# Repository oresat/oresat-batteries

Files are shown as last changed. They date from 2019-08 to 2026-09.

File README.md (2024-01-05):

# OreSat Battery Card

This is the battery card for the OreSat system. You can have up to four of these cards in any OreSat system, ID is set by resistors.

## Version History

- v1.0: We don't talk about v1 (EAGLE).
- v2.0: First true pack with 3D printed cell storage. Many small issues (EAGLE).
- v3.0: Flight ready pack, flown 2021-03-15 on OreSat0. Worked! (EAGLE).
- v3.1: Imported into KiCAD, small tweaks in process (KiCAD).

## Bill of Materials

- [PCBA](https://docs.google.com/spreadsheets/d/11vG1kWyrAjmbF5QJM-EhXmvQoF6O47japwYlHF802do/edit#gid=576852939)
- [Assembly](https://docs.google.com/spreadsheets/d/1GmZE2MR5q2XFSR2Y-65dwwPd7tem3i0CEjZBlCLeJBU/edit?usp=sharing)

## Mechanical CAD

- In [OnShape](https://cad.onshape.com/documents/5eda02ab87dc9021603c3619/w/adac4deb8bbe537007a3b153/e/e3b4fa777f54f6382aedf8d8).

## Technical Information

- 2 independent 2S1P 18650 battery packs (4 batteries total, in 2 packs). Each pack has:
   - Battery protection circuitry for charge and discharge control for each 2S1P pack
   - MAX17500 fuel gauge with cell balancing and cell temperature monitoring
- 3D printed battery holder, designed for CRP Windform SLS Nylon material (OK with Form3 Flame Retardant Resin).
- Positive battery lead disconnection switches (with room for plunger assemblies that go through OreSat +/-X rails).
- Satellite shutdown switches (!SHUTDOWN) (with room for plunger assemblies that go through OreSat +/-X rails).
- Flexible polyimide heater tapes to keep batteries above 0 C
- STM32F091 microcontroller (controlled by the OreSat Power Domain) to interface everything to the CAN bus

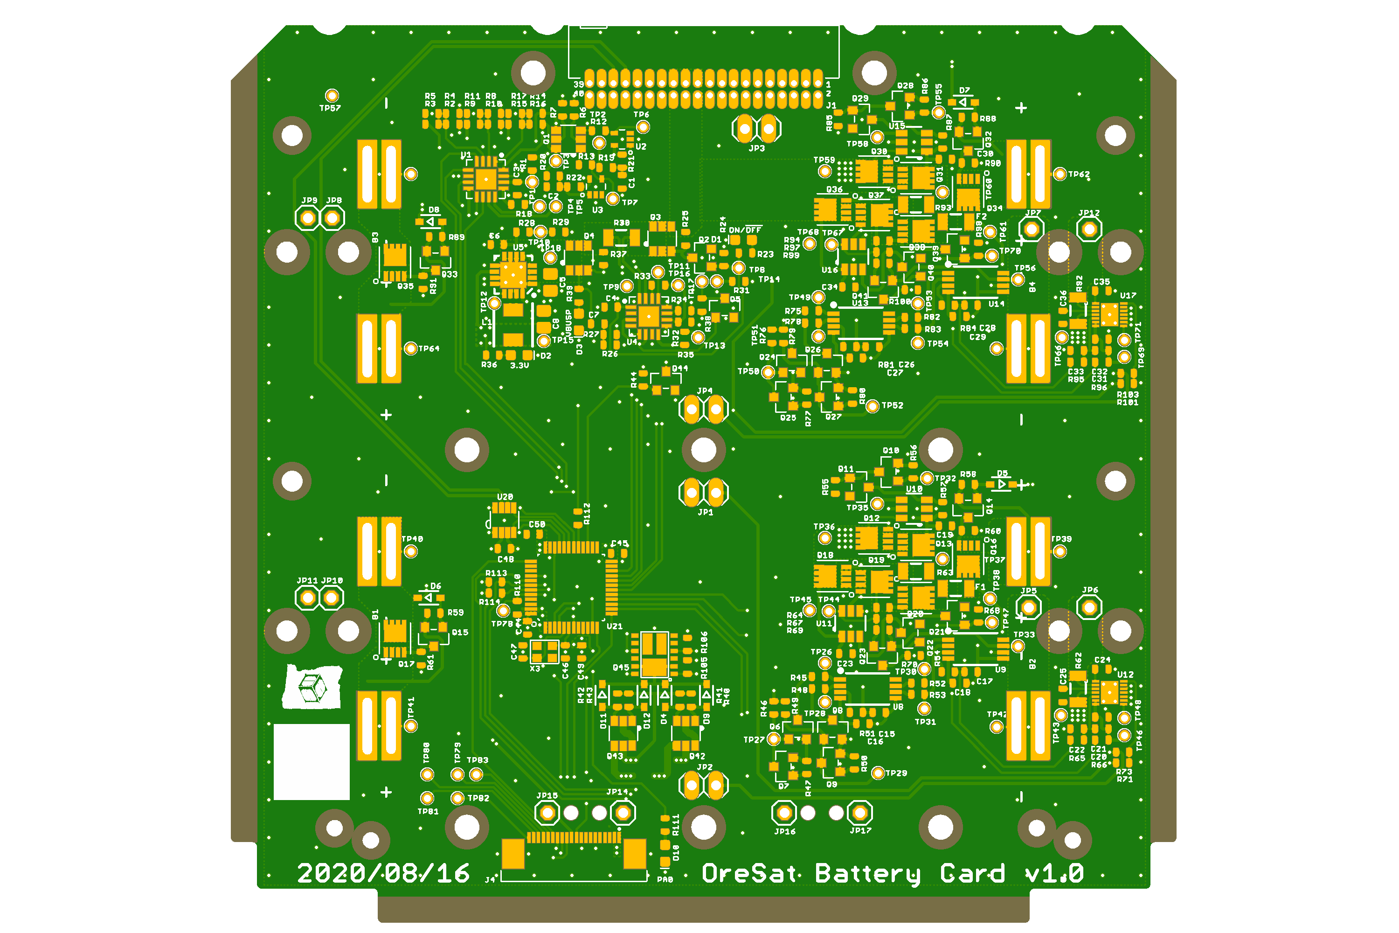
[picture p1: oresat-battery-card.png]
OreSat Battery Card v3.0 Picture


## TRANSITION DOCUMENT
Documentation is moving to [Google Docs](https://docs.google.com/document/d/1yaPGtJSM5RQG5k7sVpsDxBkVu4CHtm4LMNnisgOaNRg/edit#heading=h.gjdgxs). The rest of this readme will be integrated later.

## OreSat Vbus
OreSat main power bus is just our 2S Li Ion battery pack, which we've defined as 6.0 V minimum, 7.2 V typical, and 8.4 V maximum. Everything is directly connected to that bus, including:

- Other Oreat battery cards. For >= 2U CubeSats, you'll probably have at least two battery cards.
- All solar panels. Thus the solar panels see the direct battery voltage and can dump directly into the battery packs, thus doing _actual_ MPPT.
- All loads.

## Battery Card Topology
Confusingly, Each OreSat battery card has 2 independent battery packs on it. Each pack is made of a 2S1P 18650 LiPo cell pack. So it's a 2x2S1P if you will. Despite this, each card is independent and the OPD is fully capable of functioning with only one active card.

We decided to separate the packs instead of combining them into a single 2S2P pack for the sake of redundancy, we can lose one cell and the other pack can still provide power to the OPD, as opposed to losing an entire card from a single cell failure.  This design does come with the added drawbacks of extra overhead in the form of requiring more charge protection and fuel gauge circuitry.

## Charge/Discharge Protection
We are using Ablic S8209 to monitor our cell voltage levels and disable charging if the cell voltage goes above the predetermined overcharging threshold or disable discharging if the cell voltage goes below a predetermined discharging threshold.

The S8209 has two inputs that, if activated, will trigger the either the over-charge or under-charge protection to activate.  This allows us to daisy chain these chips together, so that each cell has its own charge protection IC.  It also allows us to connect them to a GPIO on an onboard microcontroller so that we can manually disable charging or discharging functionality if needed.  Below is a state diagram that depicts the desired behavior of our charging and discharging protection circuit

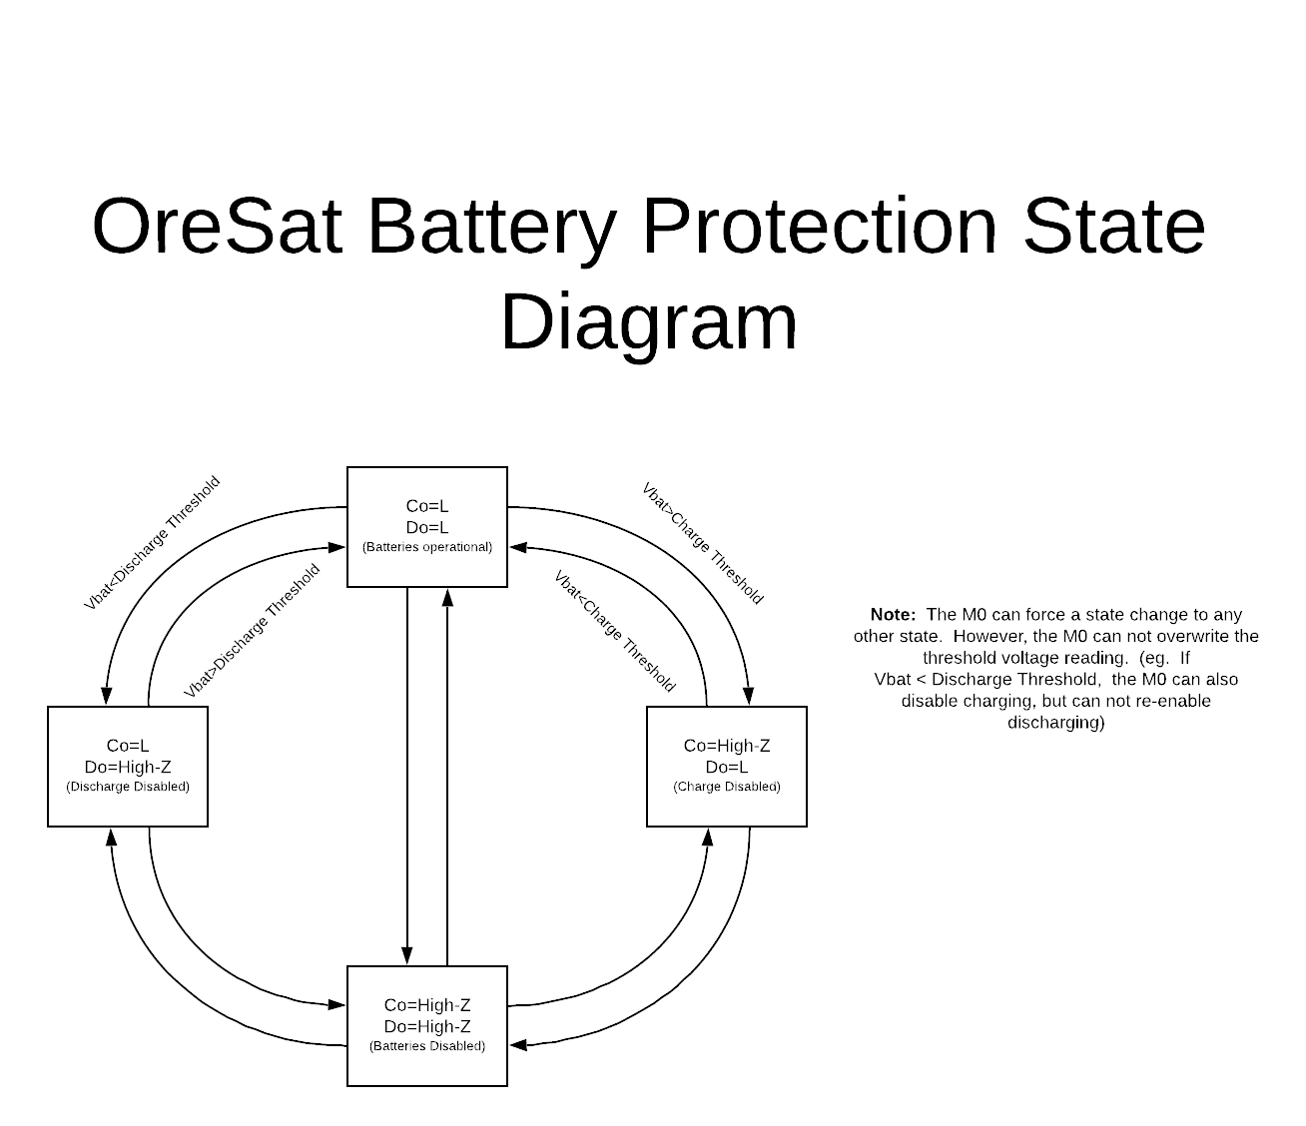
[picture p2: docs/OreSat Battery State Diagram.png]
Battery Disable State Diagram


The output of the S8209 uses an internal N-channel MOSFET, which has the potential to latch from radiation exposure.   To combat this, we have P-channel MOSFETS in series with the VDD of each S8209, the gate of the MOSFET is connected to our onboard microcontroller, so that we can periodically power cycle the S8209 and clear the N-channel latch.

The actual control of charge and discharge are done using Linear LTC4412 ideal diode controllers. Totally bizarre, but indepdenently controllable!

## Fuel Gauge and Cell Health Monitoring
Each 2S1P battery back will have two MAX17205 fuel gauges to monitor the packs current state of charge, and the long term health of the battery.  Each MAX17205 will be reporting both the direct State of charge (in mAh) and the percentage over I2C to our M0, compensating for factors such as cell degradation and temperature ranges.  We are still testing the accuracy of the MAX17205's compensation algorithm's for extreme charge levels and temperature in our lab.  At this point we don't know how much we should be relying on these compensation algorithms, they could be amazing! Or horrible! We don't know! Yay science!

Each fuel gauge is also monitoring the battery temperatures with a single internal sensor and two external thermistors (we are still determining the best position for these thermistors).  This gives us a wackton of data which is good because we are data hoarders.

Finally the MAX17205 also does cell balancing, which we'll enable while charging.

## Heaters
Thermal models of both 1U and 2U CubeSats show an average "passive" battery temperature of ~ -10 C). That's not good. We can't charge the battery below 0 C. So we've added heaters to heat up the batteries when charging if necessary.

We're using two Minco HK6903 heaters in parallel. They have "vacuum OK" (apparently?) urethane PSA that we'll use to attach them to the batteries. Note that they're 12.7 x 100 mm, and each heater goes across both batteries. At 49 ohms +/- 10% each, that's 25 ohms in parallel. Unclear on the heater's tempco. We'll ignore for now.

- At 8.4V, that's 336 mA = 2.8 W (at 100% DC)
- At 6.0V, that's 240 mA = 1.4 W (at 100% DC)
- We can of course PWM them and reduce the power as necessary

With that much current draw, we're going to need to modify the OPD circuit breaker to allow more current.

## Batteries

- Tenergy model "30005-0 (ICR 18650-2600, LR1865SK)"
- Rated at 2600 mAh
- Max voltage: 4.2 V
- Typical voltage: 3.6 V
- Minimum voltage: 2.75 V
- Maximum charge current: 1.25 A
   - 0 - 45 C only
- Maximum discharge Current:
   - -20 - 5 C = 1.25 A
   -  5 - 45 C = 5 A
   - 45 - 60 C = 3.75 A

### Temperature

Just to summarize the battery temperature operational range:

- Cell temperature < -20 C -- DEAD
- Cell temperature < 0 C -- DISCHARGE ONLY
- Cell temperature < 45 C -- NORMAL OPERATION
- Cell temperature > 45 C-- DISCHARGE ONLY
- Cell temperature > 60 C-- DEAD

### Cell failure (short)

- Short will plummet battery to < 2.5V (Vlvco) and S-8209 will disconnect the battery from discharging but not charging

## Battery pack behaviors (circuitry + firmware)

- Automatic discharge if > 6.0 V
- Automatic slow charge if < 8.4 V
- Fast charge if battery pack within ~ 0.5 V of other batteries

## Hacking the OPD Circuit Breaker

The OPD circuit breaker is supposed to trip at 300 mA without any division at the current output. Since the headers could pull up to 336, we need to probably go up to that plus 50 mA. So we put in a 10K and 20K to make a 0.66 divider and an N CH MOSFET to turn on the divider on the signal "MOARPWR". Asserting MOARPWR should give you up to 400 mA.

## LICENSE

Copyright Portland State Aerospace Society 2020.

This documentation describes Open Hardware and is licensed under the CERN OHL v. 1.2.

You may redistribute and modify this documentation under the terms of the CERN OHL v.1.2. [http://ohwr.org/cernohl](http://ohwr.org/cernohl). This documentation is distributed WITHOUT ANY EXPRESS OR IMPLIED WARRANTY, INCLUDING OF MERCHANTABILITY, SATISFACTORY QUALITY AND FITNESS FOR A PARTICULAR PURPOSE. Please see the CERN OHL v.1.2 for applicable conditions.

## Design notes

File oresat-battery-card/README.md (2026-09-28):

# "oresat-proto-card"

This is the "prototype" card for OreSat, meant to pioneer future cards and test the backplane, and be an 
easy way to hack in functionality. NOT MEANT FOR FLIGHT.

## Features

- Populates the two 1.27 mm connectors from the backplane.
- Populates all three SMPM RF connectors from the backplane.
- Standard TPS63070-bsaed buck/boost SPS (Vin = 2.5 to 7 V, Vout = 3.3V)
- Has our standard/favorite STM32F042K6 microcontroller.
   - With SWD, UART (FTDI), and CAN (to the backplane).
- Has lots of breakouts, but DO NOT POPULATE THE 0.1 IN CONNECTORS, THEY'RE TOO TALL!!!

OreSat ProtoCard Picture

## Connector information

- Main 1.27 mm connector ("Center" connector)
   - Samtec TFM-120-01-L-D-RA
   - https://www.digikey.com/products/en?lang=en&site=US&keywords=TFM-120-01-L-D-RA
   - Drawing: http://suddendocs.samtec.com/prints/tfm-1xx-xx-xxx-d-xxx-mkt.pdf
   - Brochure: http://suddendocs.samtec.com/catalog_english/tfm.pdf
   - 3D CAD: https://www.samtec.com/partnumber/tfm-120-01-l-d-ra?vendor=digikey#technical
   - Notes: the -RE1 model is better because of the solder stakes, but the female connector doesn't fit! The stakes get in the way :(

- Auxiliary 1.27 mm ("alt-left" connector)
   - Samtec TFM-110-01-L-D-RA

- RF (70 cm, L band, S band) conenctors
   - Card
      - Molex 73300-0030 (possible replacement is 73300-0020 but it has full detent that we don't want)
      - SMPM Connector Plug, Male Pin 50 Ohm Board Edge, Cutout; Surface Mount Solder, smooth bore
      - Molex w/3D: https://www.molex.com/molex/products/datasheet.jsp?part=active/0733000030_RF_COAX_CONNECTORS.xml
   - Barrell (connects card to backplane)
      - Molex 73300-0220 (alt but slightly different lengths: -0223, -0228)
      - SMPM female to female barrel adapter 
      - RF Adapters - In Series SMPM JACK/JACK BULLET .21IN
      - Molex w/3D: https://www.molex.com/molex/products/datasheet.jsp?part=active/0733000220_RF_COAX_CONNECTORS.xml

## OreSat Power Domain (OPD)

You can find more design information on the OPD [here](https://docs.google.com/document/d/1NOkO6gGEJUFRpOrkwClRlZlzWuTLteq6fP9LPf_Ez0M/edit?usp=sharing).

## LICENSE

Copyright Portland State Aerospace Society 2018.

This documentation describes Open Hardware and is licensed under the CERN OHL v. 1.2.

You may redistribute and modify this documentation under the terms of the CERN OHL v.1.2. [http://ohwr.org/cernohl](http://ohwr.org/cernohl). This documentation is distributed WITHOUT ANY EXPRESS OR IMPLIED WARRANTY, INCLUDING OF MERCHANTABILITY, SATISFACTORY QUALITY AND FITNESS FOR A PARTICULAR PURPOSE. Please see the CERN OHL v.1.2 for applicable conditions.

## Version Information

Version | Date       | Notes
--------|------------|-------------------------
3.0     | 2018/11/22 | Big changes in structure, mostly springs. Changed RF connectors to SMPM. Optimized layout for more proto area. 
2.0     | 2018/03/?? | New 1.27 mm connectors, again.
1.0     | ??         | New connectors.

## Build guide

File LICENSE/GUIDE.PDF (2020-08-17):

# Guide to the CERN OHL v.1.2

This document contains guidelines on how to apply the CERN OHL v.1.2 to a given hardware design, and on the use of hardware designs licensed under the CERN OHL v.1.2.

How to apply the CERN OHL v.1.2 to a hardware design Pre-requisite:

Authorship/ownership of the design must be clear and undisputed. Only the legal owner of the rights in the hardware design may decide under what conditions to make it available. If ownership is vested in more than one person/entity, there must be an agreement among the owners to release the hardware design as open hardware, and under the CERN OHL in particular.

The hardware design documentation and files package

Pack all your hardware design documentation files (schematics, layout...) as well as the documents listed below in an archive file. This will ensure the licensee downloads everything in one go. It is best to archive the files using a format everybody can open. Schematics and layouts should be included in both source form and a format readable by everybody, such as pdf.

The following documents must be distributed together with the hardware design documentation:

- Document containing the CERN OHL v.1.2 (e.g. LICENSE.PDF)
- This Guide
- Text files (plain ASCII file), where information can be added to but not removed from, listing:
- Contact point wishing to receive information about manufactured Products (see section 4.2) (e.g. PRODUCT.TXT);
- Modifications made by Licensee (see section 3.4.b) (e.g. CHANGES.TXT)

What to do with the hardware design documentation

Include in the hardware design documentation, for instance as a header, the following elements (see section 3.1 CERN OHL v.1.2):
- a copyright notice reflecting actual ownership;
- a notice that the hardware design documentation is licensed under the CERN OHL v.1.2, possibly with a link to http://ohwr.org/cernohl where the licence texts are hosted:
- “Licensed under CERN OHL v.1.2 or later”
- “Licensed under CERN OHL v.1.2”;
- a disclaimer of warranties;
- a Documentation Location if you wish to specify one;

The following is an example of header if CERN is the Licensor:

Copyright CERN 2013.

This documentation describes Open Hardware and is licensed under the CERN OHL v. 1.2.

You may redistribute and modify this documentation under the terms of the CERN OHL v.1.2. (http://ohwr.org/cernohl). This documentation is distributed WITHOUT ANY EXPRESS OR IMPLIED WARRANTY, INCLUDING OF MERCHANTABILITY, SATISFACTORY QUALITY AND FITNESS FOR A PARTICULAR PURPOSE. Please see the CERN OHL v.1.2 for applicable conditions

Include in a part of the Documentation corresponding to a visible part of the Product (e.g. silkscreen or top copper for a Printed Circuit Board):

- the licence notice: “Licensed under CERN OHL v.1.2”
- Do not include the CERN logo or the copyright notice
- the Documentation Location if you wish it to appear on the Product, thus enabling all subsequent recipients of the Products to find the Documentation.

How to deal with hardware designs licensed under the CERN OHL v.1.2
Generally speaking, you must always comply with any obligations applying to a particular design (detailed in a contract or accompanying licence). If you receive hardware designs licensed under the CERN OHL v.1.2, the obligations are to:
- Keep intact all the copyright and trademark notices and Documentation Location notices that are on the hardware design documentation;
- Keep intact the references to the CERN OHL v.1.2;
- Keep intact the disclaimer of warranties.

If you modify hardware design that you received from someone else that is licensed under the CERN OHL v.1.2, you must

- Keep intact all the notices referred to above;
- Include notices that you have modified the hardware designs, detailing what modifications where made (e.g. in a CHANGES.TXT file);
- Add the appropriate copyright notice and Documentation Location to the modifications that were made;
- license the modifications under the CERN OHL v.1.2 if you distribute them.

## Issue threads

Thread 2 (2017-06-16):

Surface mount 2.54 debug header pins

kwilsonpdx, 2017-06-16:
Please add surface mount header pins for VBATT/Solar Vin/Grounds/CANH/CANL/UARTRX/UARTTX. You could route these to one 2x8 or separate around board as layout permits. These can be DNP for flight.

austinjoseph, 2017-06-21:
Added to a single debug 2x8 2.54mm pinheader.  Will go out in next commit.

Closed 2017-06-21.

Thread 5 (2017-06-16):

Test issue: Suggest adding Thermocouple attach point for analysis

kwilsonpdx, 2017-06-16:
To test heater performance suggest adding at least one thermocouple attach point. I'm thinking a #2 through hole. Open to suggestions on implementation.

(I'm not sure the internal battery thermistor is going to give us what we need to test the resistive heater).

Closed 2020-08-17.

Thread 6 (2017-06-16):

Review source for SCL/SDA pullup resistors

kwilsonpdx, 2017-06-16:
Should the source be VBATT+ not VSOLAR?

austinjoseph, 2017-06-21:
Ha!  You're right.  If we run it from the solar panels we lose telemetry when that panel is on the dark side.  I've fixed this issue and will push it soon.

Closed 2017-06-21.

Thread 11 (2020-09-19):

Add 100k Pullups to the LT4412 STAT pin

davidalay, 2020-09-19:
the pin is an open collector, when active it can sink max of 10uA of current so pullup must be >10k

andrewgreenberg, 2021-04-08:
Nope! The uC will use weak pullups to 3.3V for these puppies. I'll tell Dave.

Closed 2021-04-08.

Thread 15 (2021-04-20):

Fixes to the battery board based on v2.1 assembly

andrewgreenberg, 2021-04-20:
Ref designators : C29, C28, R27, R17, R14
TP12 shorts to the inductor - move it!

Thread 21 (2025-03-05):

MAX17205 isn't calculating the correct capacity

andrewgreenberg, 2025-03-05:
This is probably a firmware issue, but the MAX17205 is not calculating the correct capacity of the battery pack. Voltage and current seem to be working, and the pack "factory" capacity is correct, but it's not updating the capacity in any meaningful way. Is the MAX losing it's mind every time we hit the !SHUTDOWN circuit because it's disconnected from the battery? And it wasn't designed for that? Have we misconfigured it some way? Is it that the battery is never turned off long enough for the MAX to get a Voc reading?

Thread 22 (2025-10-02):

POUT signal not routed to an analog input

plskeggs, 2025-10-02:
The following is about the STM32F091 version of the battery card.

The POUT signal that can measure power/current draw from OPD goes to PA8, and is an analog signal 0-1.2v according to the schematic. However, PA8 does not connect to any ADC channel in the F091. The only unused ADC-capable pin is PA6, pin 16. As a result, the Oresat 0 and 0.5 firmware does not monitor this signal.

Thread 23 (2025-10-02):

F091 not labelled on schematic

plskeggs, 2025-10-02:
It is missing "U21 ST32F091CCT7."

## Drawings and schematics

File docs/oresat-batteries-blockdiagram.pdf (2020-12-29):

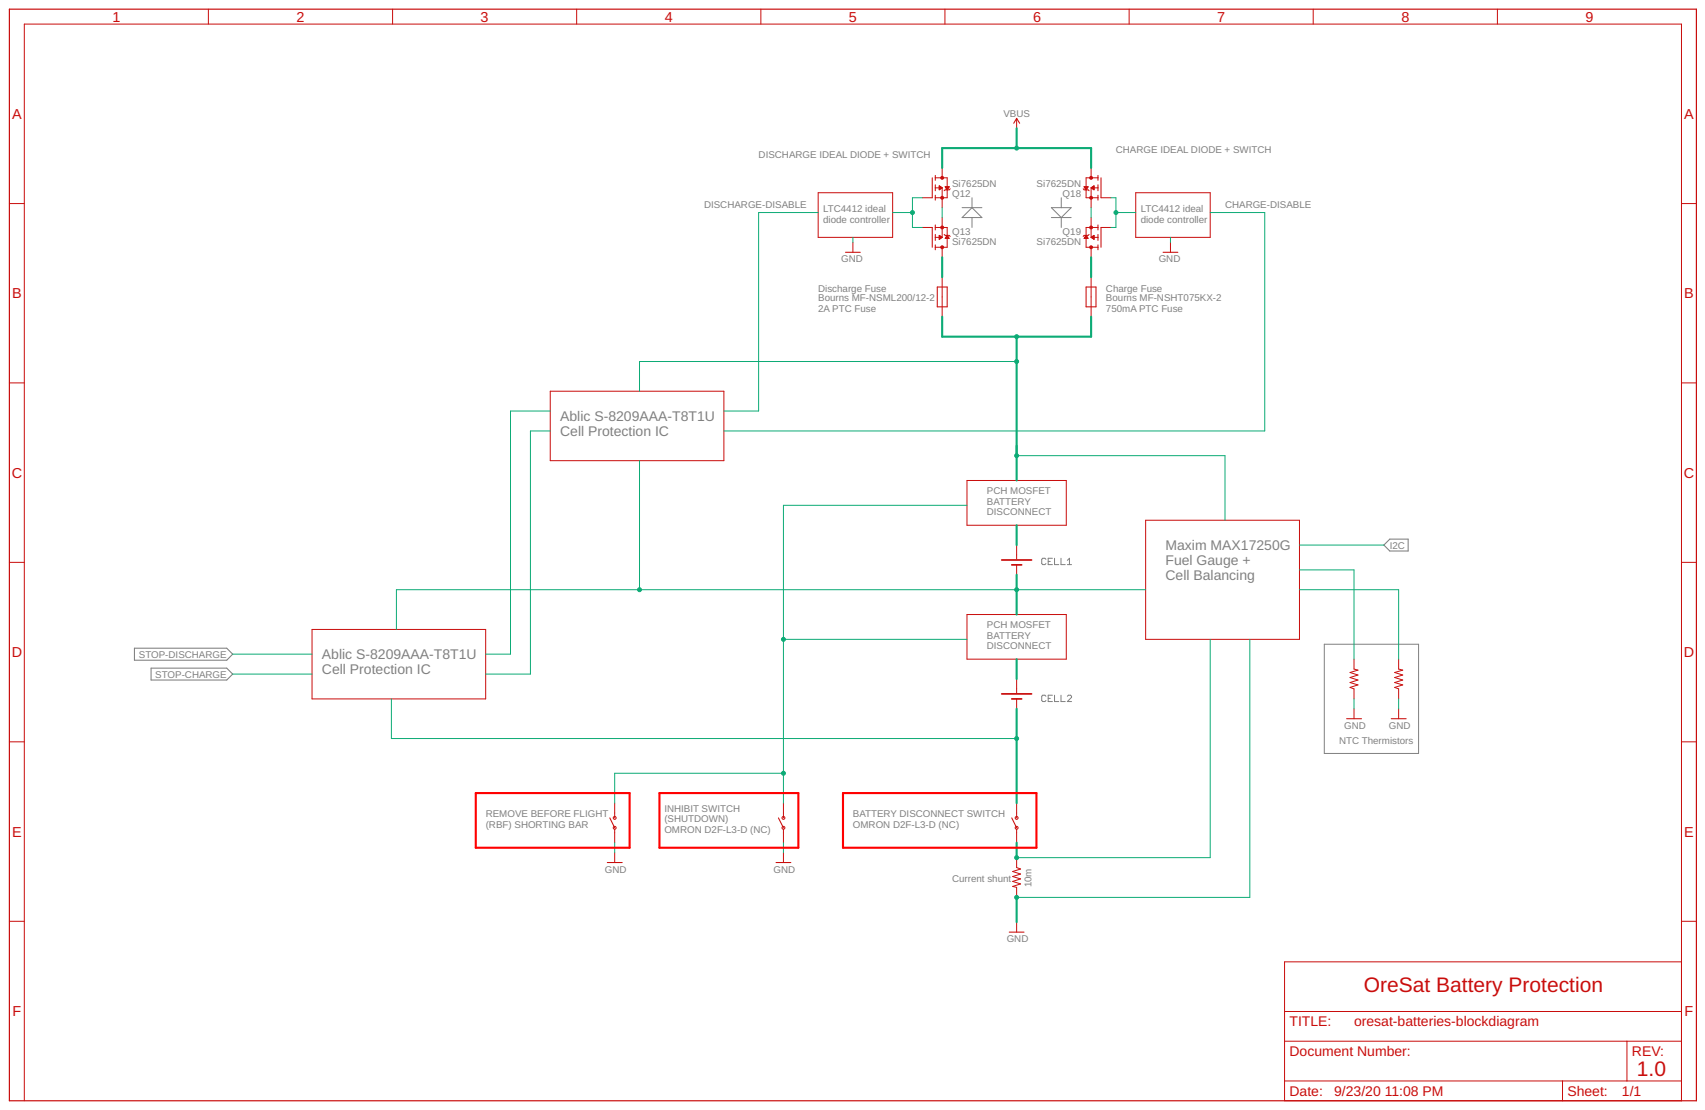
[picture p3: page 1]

CHARGE IDEAL DIODE + SWITCH DISCHARGE IDEAL DIODE + SWITCH

LTC4412 ideal diode controller Bourns MF-NSML200/12-2

PCH MOSFET BATTERY DISCONNECT

Maxim MAX17250G
Fuel Gauge + Cell Balancing

NTC Thermistors BATTERY DISCONNECT SWITCH OMRON D2F-L3-D (NC)

(SHUTDOWN) OMRON D2F-L3-D (NC) REMOVE BEFORE FLIGHT
(RBF) SHORTING BAR

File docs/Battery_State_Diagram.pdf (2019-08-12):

# OreSat Battery Protection State Diagram

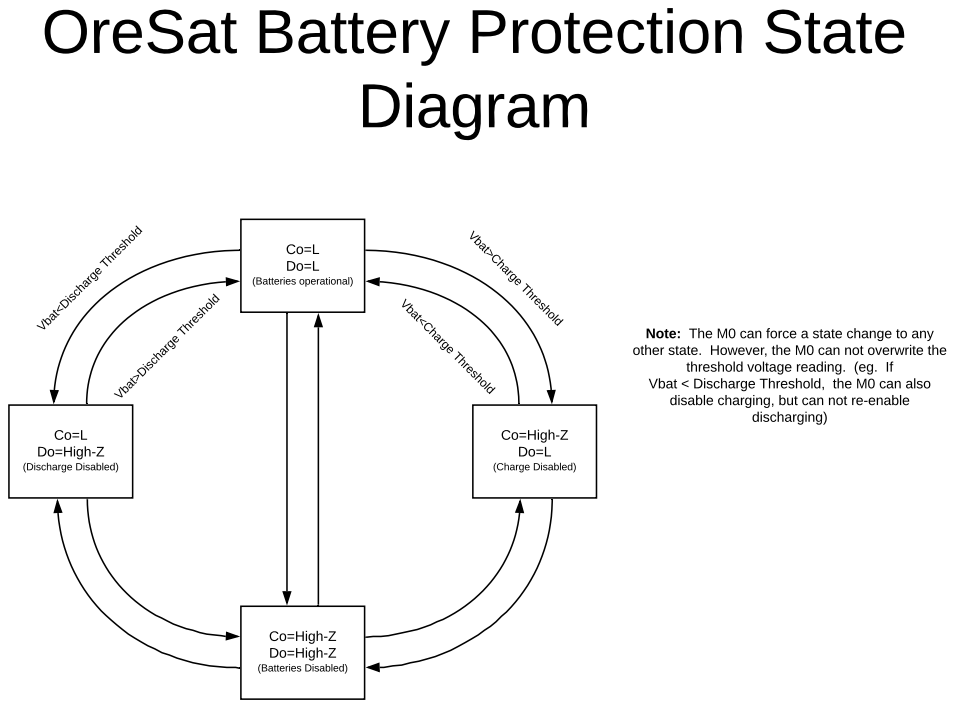
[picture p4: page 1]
Co=L Do=L (Batteries operational); Co=L Do=High-Z (Discharge Disabled); Co=High-Z Do=L (Charge Disabled); Co=High-Z Do=High-Z (Batteries Disabled); discharging)

Vbat>Charge Threshold

Vbat<Charge Threshold

Vbat<Discharge Threshold

Note: The M0 can force a state change to any
other state. However, the M0 can not overwrite the

threshold voltage reading. (eg. If
Vbat < Discharge Threshold, the M0 can also
disable charging, but can not re-enable

Vbat>Discharge Threshold

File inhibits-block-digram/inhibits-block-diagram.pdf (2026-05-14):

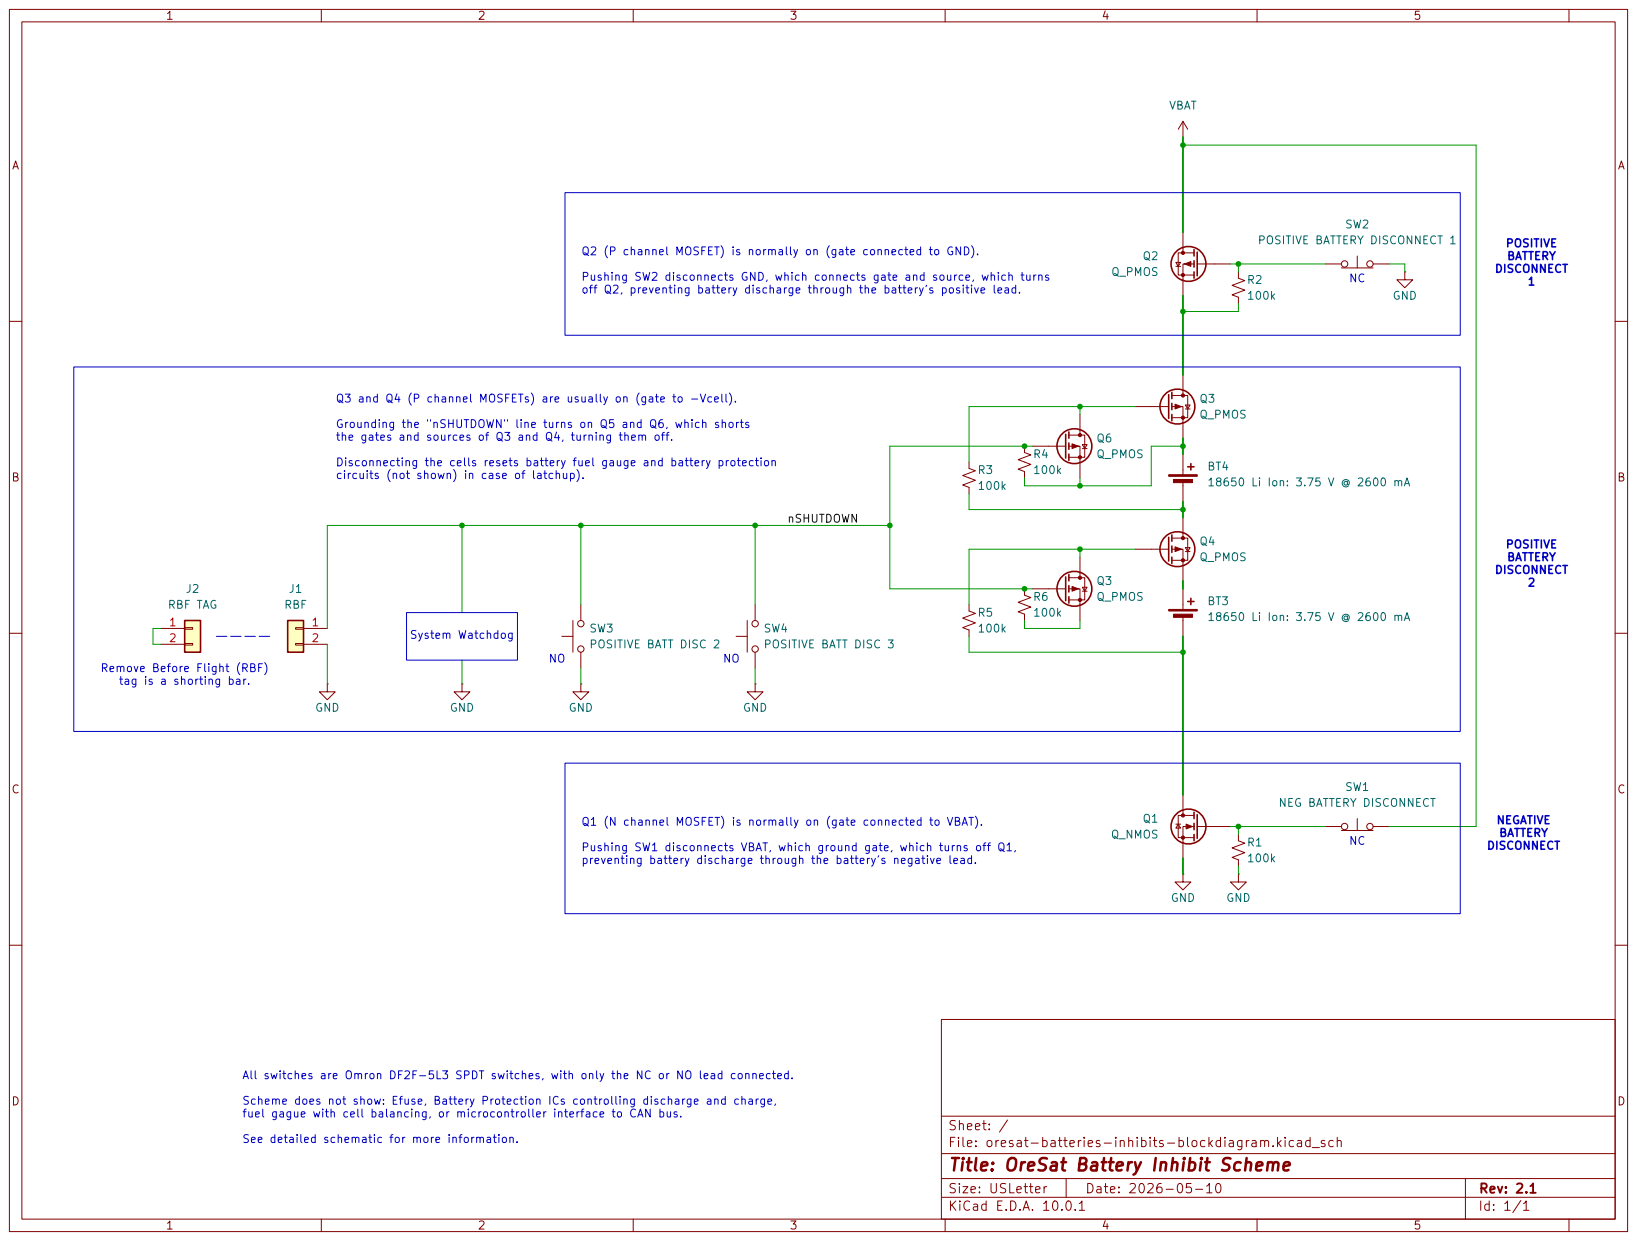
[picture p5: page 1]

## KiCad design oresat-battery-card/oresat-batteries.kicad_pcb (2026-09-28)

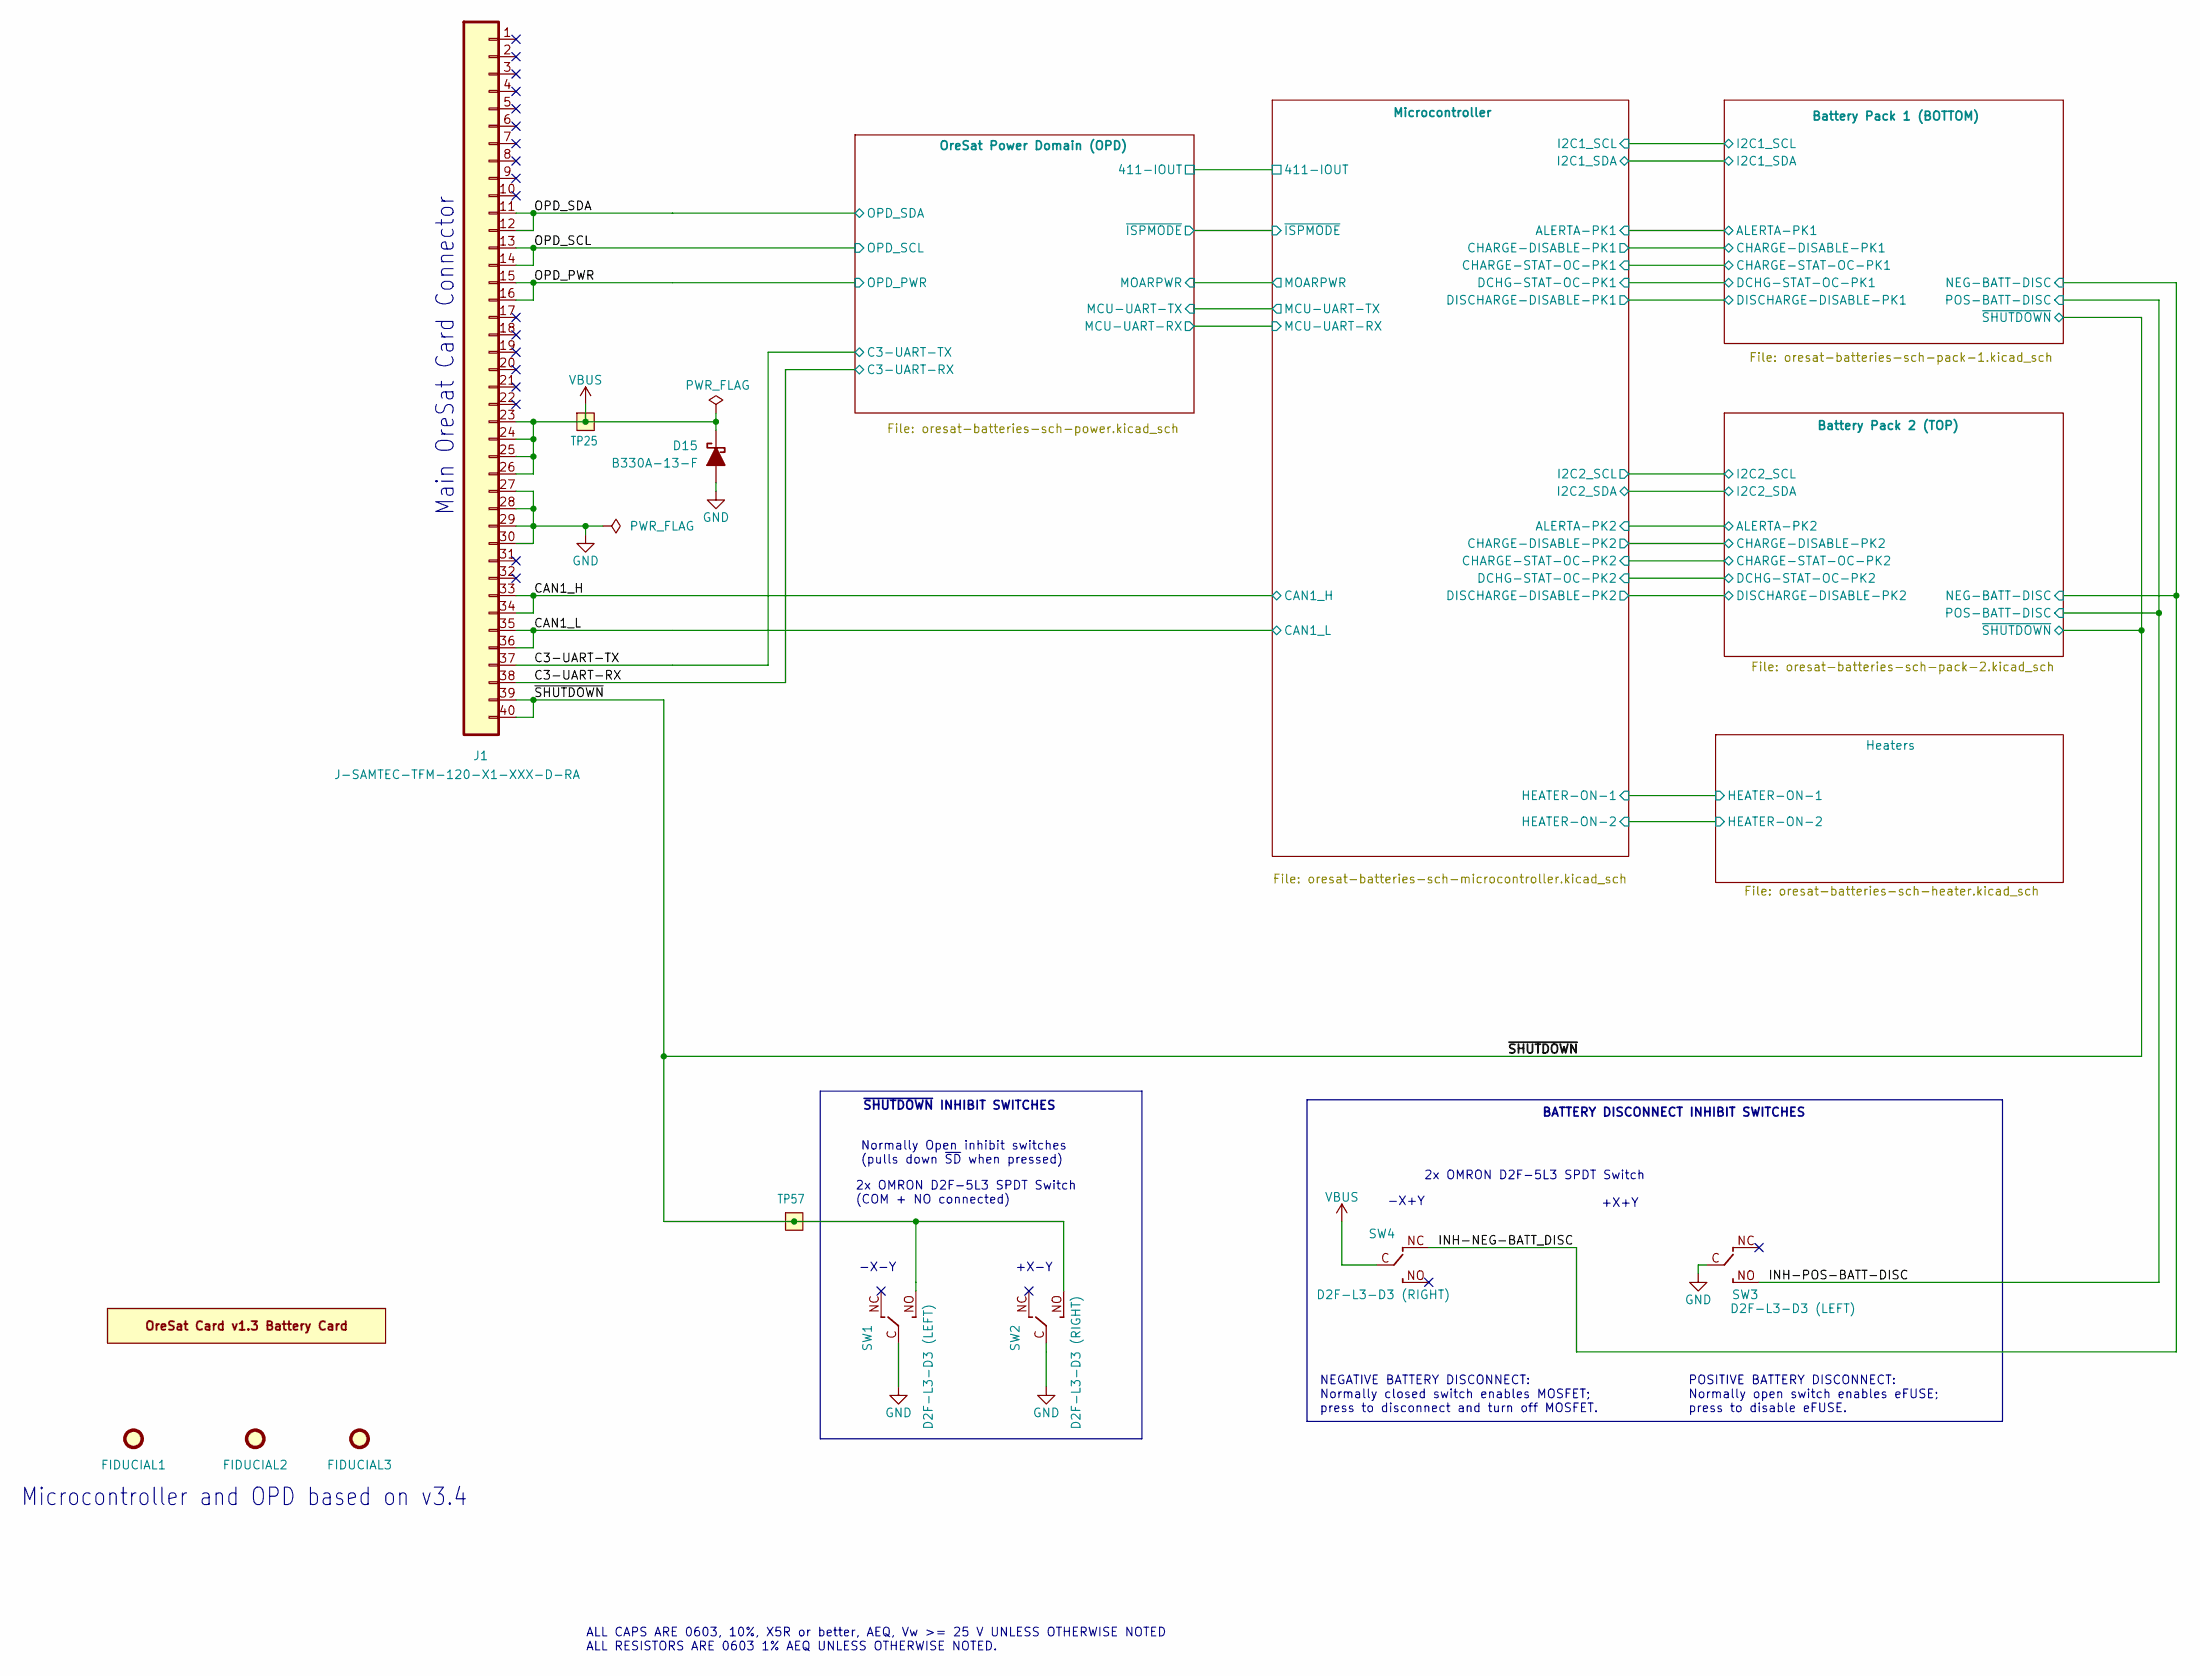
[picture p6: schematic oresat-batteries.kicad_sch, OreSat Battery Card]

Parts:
D15: B330A-13-F; D_SMA; MPN B330A-13-F
FIDUCIAL1, FIDUCIAL2, FIDUCIAL3: FIDUCIAL-1.0X2.0; Fiducial_1mm_Mask2mm
J1: J-SAMTEC-TFM-120-X1-XXX-D-RA; MPN TFM-120-01-L-D-RA
PCB1: ORESAT-CARD-V1.3-BATTERY; ORESAT-CARD-V1.3-BATTERY-V3.0; MPN N/A
SW1, SW3: D2F-L3-D3 (LEFT); D2F-L3-D3-HORIZONTAL-L; MPN D2F-L3-D3
SW2, SW4: D2F-L3-D3 (RIGHT); D2F-L3-D3-HORIZONTAL-R; MPN D2F-L3-D3
TP25, TP57: TEST-POINT-LARGE-SQUARE; TestPoint-0.75mm-th

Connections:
/C3-UART-RX: J1.38; also elsewhere on the board
/C3-UART-TX: J1.37; also elsewhere on the board
/CAN1_H: J1.33, J1.34; also elsewhere on the board
/CAN1_L: J1.35, J1.36; also elsewhere on the board
/INH-NEG-BATT_DISC: SW4.NC; also elsewhere on the board
/INH-POS-BATT-DISC: SW3.NO; also elsewhere on the board
/OPD_PWR: J1.15, J1.16; also elsewhere on the board
/OPD_SCL: J1.13, J1.14; also elsewhere on the board
/OPD_SDA: J1.11, J1.12; also elsewhere on the board
/~SHUTDOWN: J1.39, J1.40, SW1.NO, SW2.NO, TP57.1 (1_1); also elsewhere on the board
GND: D15.2 (A), J1.27, J1.28, J1.29, J1.30, SW1.C (COM), SW2.C (COM), SW3.C (COM); also elsewhere on the board
VBUS: D15.1 (K), J1.23, J1.24, J1.25, J1.26, SW4.C (COM), TP25.1 (1_1); also elsewhere on the board

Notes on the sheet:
Normally Open inhibit switches (pulls down ~{SD} when pressed)
Main OreSat Card Connector
~{SHUTDOWN} INHIBIT SWITCHES
BATTERY DISCONNECT INHIBIT SWITCHES
+X+Y
2x OMRON D2F-5L3 SPDT Switch (COM + NO connected)
-X-Y
ALL CAPS ARE 0603, 10%, X5R or better, AEQ, Vw >= 25 V UNLESS OTHERWISE NOTED ALL RESISTORS ARE 0603 1% AEQ UNLESS OTHERWISE NOTED.
+X-Y
-X+Y
Microcontroller and OPD based on v3.4
NEGATIVE BATTERY DISCONNECT: Normally closed switch enables MOSFET; press to disconnect and turn off MOSFET.
2x OMRON D2F-5L3 SPDT Switch
POSITIVE BATTERY DISCONNECT: Normally open switch enables eFUSE; press to disable eFUSE.

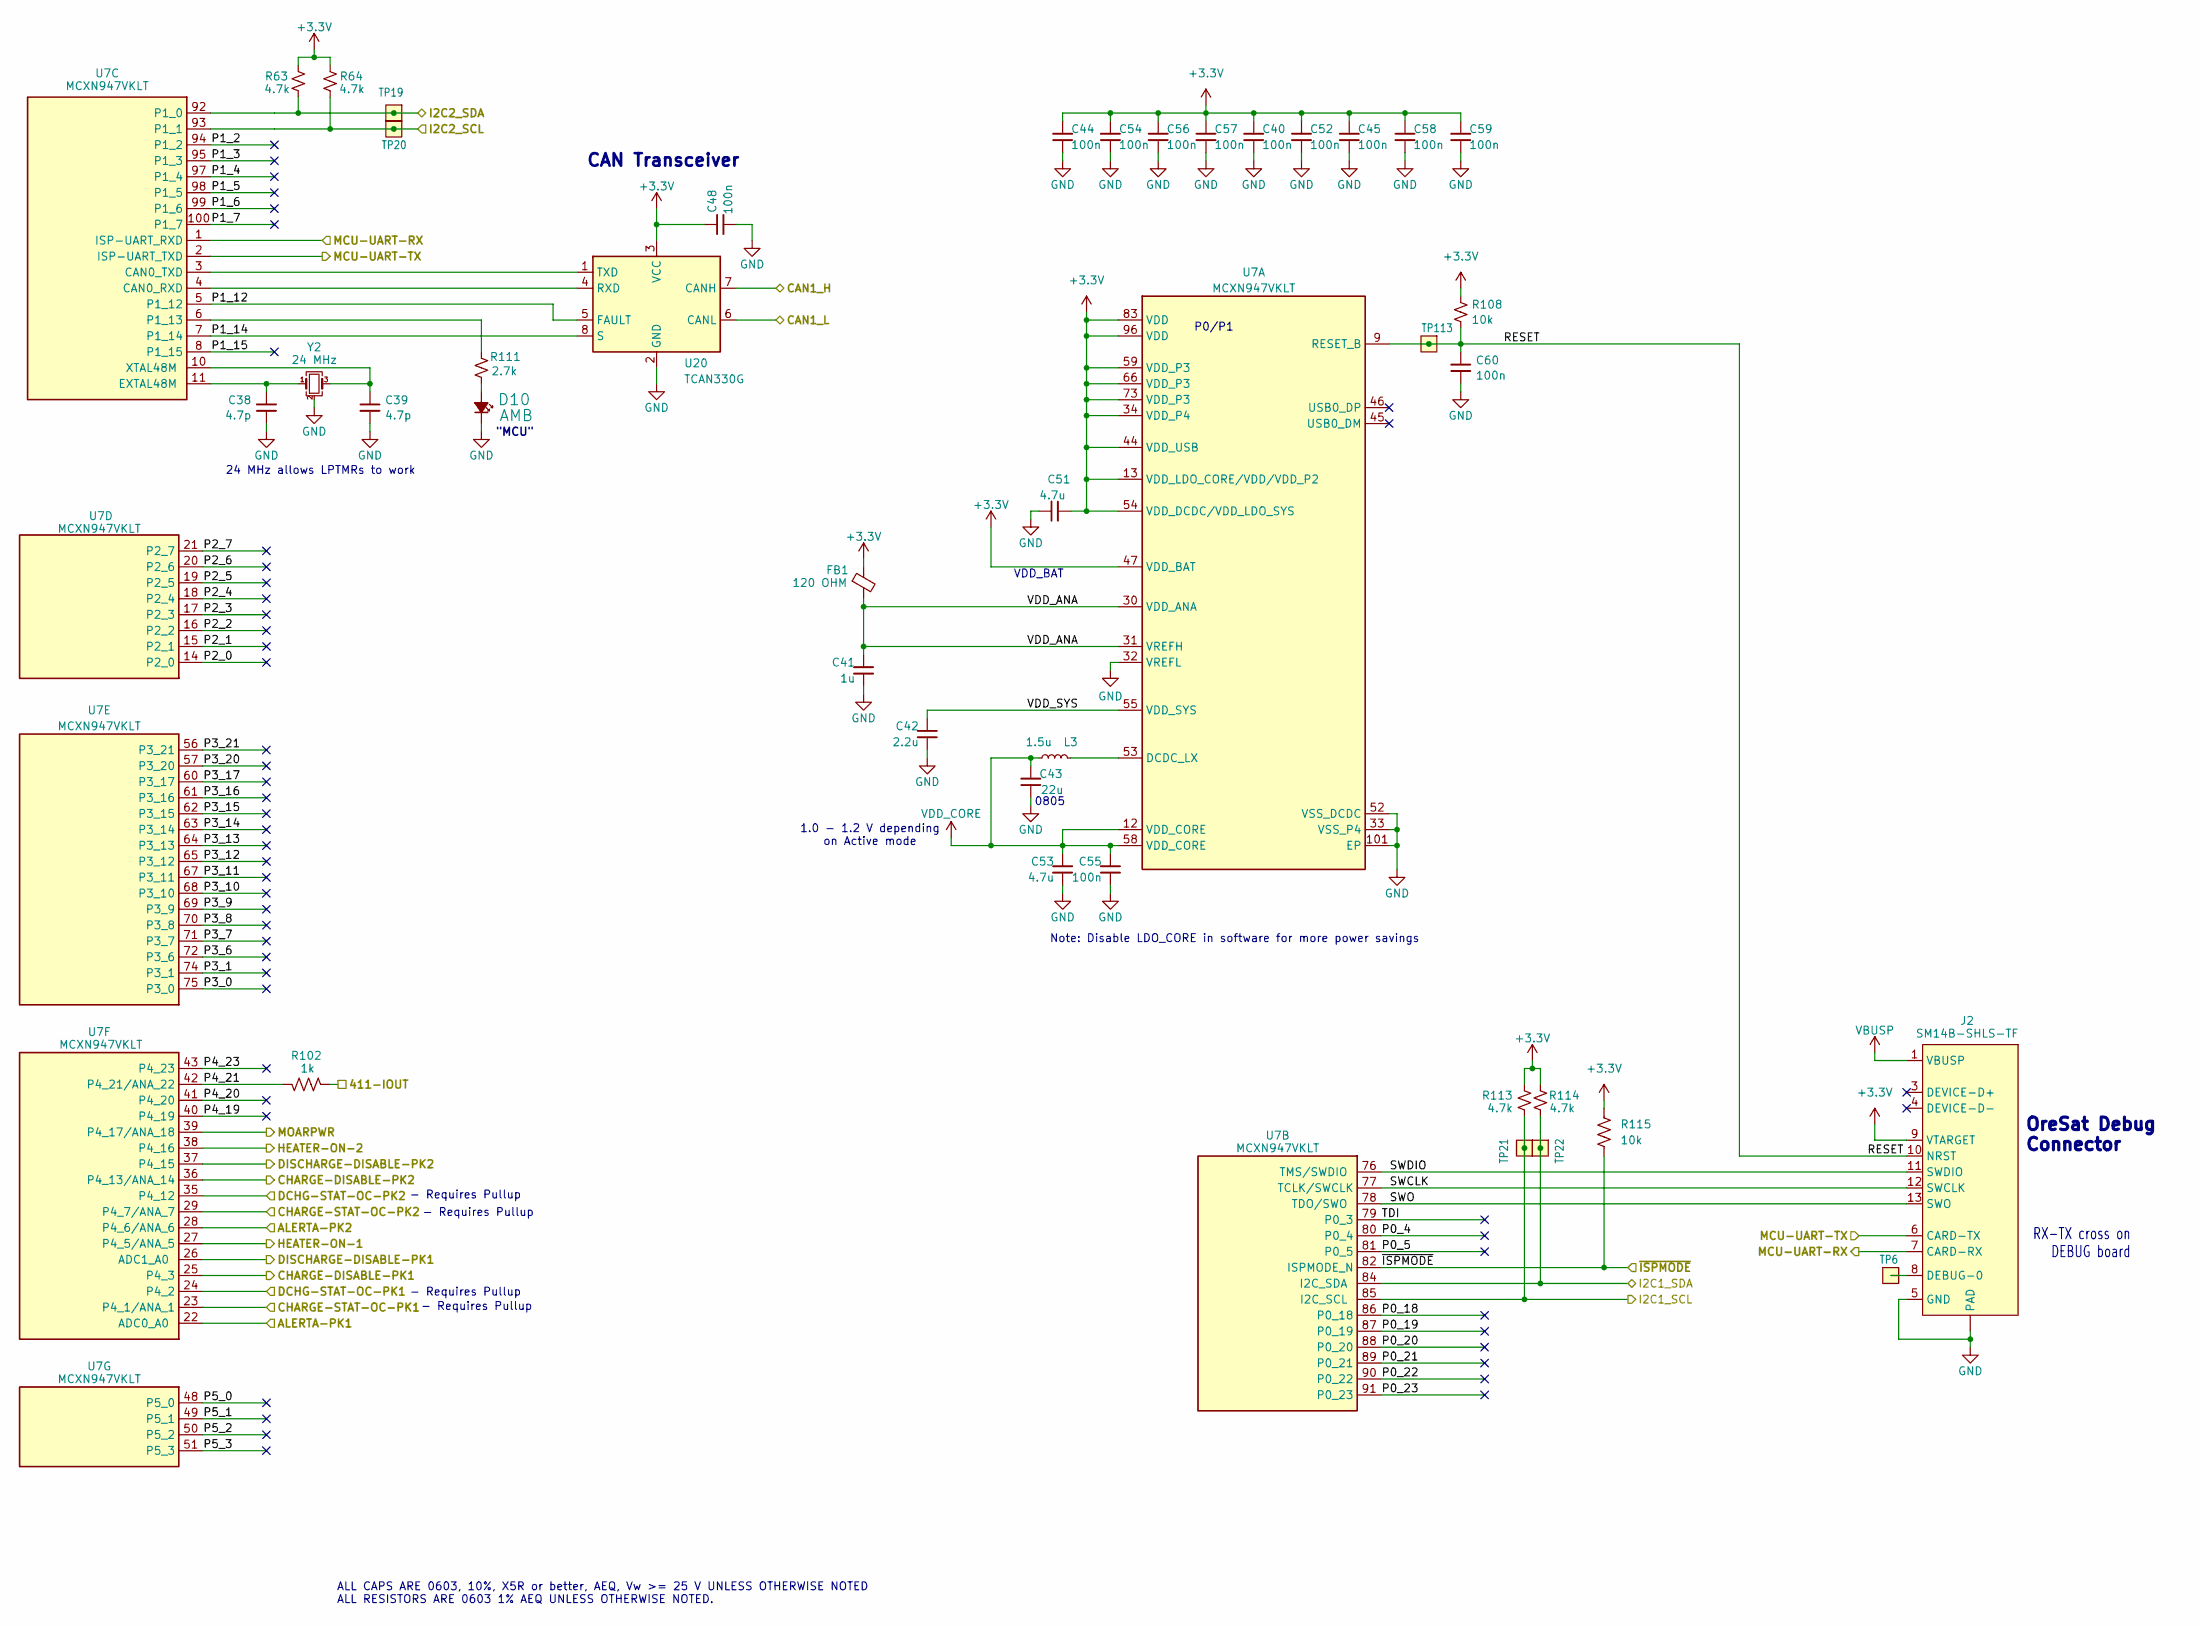
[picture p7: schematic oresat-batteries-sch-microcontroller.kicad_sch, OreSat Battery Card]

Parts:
C38, C39: 4.7p; 0603-C-NOSILK; MPN C0603C479D5GACAUTO
C40, C44, C45, C48, C52, C54, C55, C56, C57, C58, C59, C60: 100n; 0603-C-NOSILK; MPN C0603C104K5RACAUTO
C41: 1u; 0603-C-NOSILK; MPN GRT188R71E105KE13D
C42: 2.2u; 0603-C-NOSILK; MPN GRT188C71E225KE13D
C43: 22u; 0805-C-NOSILK; MPN GRT21BC81C226ME13L
C51, C53: 4.7u; 0603-C-NOSILK; MPN GRT188C71C475KE13D
D10: AMB; LED_0603_1608Metric; MPN 150060AS75000
FB1: 120 OHM; 0805-B-NOSILK; MPN 2508051217Y6
J2: SM14B-SHLS-TF; J-JST-SM14BSHLSTF; MPN SM14B-SHLS-TF
L3: 1.5u; L_0805_2012Metric; MPN SRP2012TMA-1R5M
R63, R64, R113, R114: 4.7k; 0603-C-NOSILK; MPN RMCF0603FT4K70
R102: 1k; 0603-C-NOSILK; MPN RMCF0603FT1K00
R108, R115: 10k; 0603-C-NOSILK; MPN RMCF0603FT10K0
R111: 2.7k; 0603-C-NOSILK; MPN RMCF0603FT2K70
TP6, TP113: Test-Point; TestPoint-0.75mm-th
TP19, TP20, TP21, TP22: TEST-POINT-LARGE-SQUARE; TestPoint-0.75mm-th
U7: MCXN947VKLT; MCXN947KVLT-QFP50P1600X1600X160-101N; MPN MCXN947VKLT
U20: TCAN330G; SOT-23-8; MPN TCAN330GDCNT
Y2: 24 MHz; Crystal_SMD_2016-4Pin_2.0x1.6mm; MPN 830108212309

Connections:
+3.3V: C40.1, C44.1, C45.1, C48.2, C51.1, C52.1, C54.1, C56.1, C57.1, C58.1, C59.1, FB1.1, J2.9 (VTARGET), R63.2, R64.2, R108.2, R113.2, R114.2, R115.2, U7.13 (VDD_LDO_CORE/VDD/VDD_P2), U7.34 (VDD_P4), U7.44 (VDD_USB), U7.47 (VDD_BAT), U7.54 (VDD_DCDC/VDD_LDO_SYS), U7.59 (VDD_P3), U7.66 (VDD_P3), U7.73 (VDD_P3), U7.83 (VDD), U7.96 (VDD), U20.3 (VCC); also elsewhere on the board
/Battery Pack 1 (BOTTOM)/ALERTA-PK1: U7.22 (ADC0_A0); also elsewhere on the board
/Battery Pack 1 (BOTTOM)/CHARGE-DISABLE-PK1: U7.25 (P4_3); also elsewhere on the board
/Battery Pack 1 (BOTTOM)/CHARGE-STAT-OC-PK1: U7.23 (P4_1/ANA_1); also elsewhere on the board
/Battery Pack 1 (BOTTOM)/DCHG-STAT-OC-PK1: U7.24 (P4_2); also elsewhere on the board
/Battery Pack 1 (BOTTOM)/DISCHARGE-DISABLE-PK1: U7.26 (ADC1_A0); also elsewhere on the board
/Battery Pack 1 (BOTTOM)/I2C1_SCL: R113.1, TP21.1 (1_1), U7.85 (I2C_SCL); also elsewhere on the board
/Battery Pack 1 (BOTTOM)/I2C1_SDA: R114.1, TP22.1 (1_1), U7.84 (I2C_SDA); also elsewhere on the board
/Battery Pack 2 (TOP)/ALERTA-PK2: U7.28 (P4_6/ANA_6); also elsewhere on the board
/Battery Pack 2 (TOP)/CHARGE-DISABLE-PK2: U7.36 (P4_13/ANA_14); also elsewhere on the board
/Battery Pack 2 (TOP)/CHARGE-STAT-OC-PK2: U7.29 (P4_7/ANA_7); also elsewhere on the board
/Battery Pack 2 (TOP)/DCHG-STAT-OC-PK2: U7.35 (P4_12); also elsewhere on the board
/Battery Pack 2 (TOP)/DISCHARGE-DISABLE-PK2: U7.37 (P4_15); also elsewhere on the board
/Battery Pack 2 (TOP)/I2C2_SCL: R64.1, TP20.1 (1_1), U7.93 (P1_1); also elsewhere on the board
/Battery Pack 2 (TOP)/I2C2_SDA: R63.1, TP19.1 (1_1), U7.92 (P1_0); also elsewhere on the board
/CAN1_H: U20.7 (CANH); also elsewhere on the board
/CAN1_L: U20.6 (CANL); also elsewhere on the board
/Heaters/HEATER-ON-1: U7.27 (P4_5/ANA_5); also elsewhere on the board
/Heaters/HEATER-ON-2: U7.38 (P4_16); also elsewhere on the board
/Microcontroller/411-IOUT: R102.2; also elsewhere on the board
/Microcontroller/MCU-UART-RX: J2.7 (CARD-RX), U7.1 (ISP-UART_RXD); also elsewhere on the board
/Microcontroller/MCU-UART-TX: J2.6 (CARD-TX), U7.2 (ISP-UART_TXD); also elsewhere on the board
/Microcontroller/MOARPWR: U7.39 (P4_17/ANA_18); also elsewhere on the board
/Microcontroller/P0_4: U7.80 (P0_4)
/Microcontroller/P0_5: U7.81 (P0_5)
/Microcontroller/P0_18: U7.86 (P0_18)
/Microcontroller/P0_19: U7.87 (P0_19)
/Microcontroller/P0_20: U7.88 (P0_20)
/Microcontroller/P0_21: U7.89 (P0_21)
/Microcontroller/P0_22: U7.90 (P0_22)
/Microcontroller/P0_23: U7.91 (P0_23)
/Microcontroller/P1_2: U7.94 (P1_2)
/Microcontroller/P1_3: U7.95 (P1_3)
/Microcontroller/P1_4: U7.97 (P1_4)
/Microcontroller/P1_5: U7.98 (P1_5)
/Microcontroller/P1_6: U7.99 (P1_6)
/Microcontroller/P1_7: U7.100 (P1_7)
/Microcontroller/P1_12: U7.5 (P1_12), U20.5 (FAULT)
/Microcontroller/P1_14: U7.7 (P1_14), U20.8 (S)
/Microcontroller/P1_15: U7.8 (P1_15)
/Microcontroller/P2_0: U7.14 (P2_0)
/Microcontroller/P2_1: U7.15 (P2_1)
/Microcontroller/P2_2: U7.16 (P2_2)
/Microcontroller/P2_3: U7.17 (P2_3)
/Microcontroller/P2_4: U7.18 (P2_4)
/Microcontroller/P2_5: U7.19 (P2_5)
/Microcontroller/P2_6: U7.20 (P2_6)
/Microcontroller/P2_7: U7.21 (P2_7)
/Microcontroller/P3_0: U7.75 (P3_0)
/Microcontroller/P3_1: U7.74 (P3_1)
/Microcontroller/P3_6: U7.72 (P3_6)
/Microcontroller/P3_7: U7.71 (P3_7)
/Microcontroller/P3_8: U7.70 (P3_8)
/Microcontroller/P3_9: U7.69 (P3_9)
/Microcontroller/P3_10: U7.68 (P3_10)
/Microcontroller/P3_11: U7.67 (P3_11)
/Microcontroller/P3_12: U7.65 (P3_12)
/Microcontroller/P3_13: U7.64 (P3_13)
/Microcontroller/P3_14: U7.63 (P3_14)
/Microcontroller/P3_15: U7.62 (P3_15)
/Microcontroller/P3_16: U7.61 (P3_16)
/Microcontroller/P3_17: U7.60 (P3_17)
/Microcontroller/P3_20: U7.57 (P3_20)
/Microcontroller/P3_21: U7.56 (P3_21)
/Microcontroller/P4_19: U7.40 (P4_19)
/Microcontroller/P4_20: U7.41 (P4_20)
/Microcontroller/P4_21: R102.1, U7.42 (P4_21/ANA_22)
/Microcontroller/P4_23: U7.43 (P4_23)
/Microcontroller/P5_0: U7.48 (P5_0)
/Microcontroller/P5_1: U7.49 (P5_1)
/Microcontroller/P5_2: U7.50 (P5_2)
/Microcontroller/P5_3: U7.51 (P5_3)
/Microcontroller/RESET: C60.1, J2.10 (NRST), R108.1, TP113.1 (1_1), U7.9 (RESET_B)
/Microcontroller/SWCLK: J2.12 (SWCLK), U7.77 (TCLK/SWCLK)
/Microcontroller/SWDIO: J2.11 (SWDIO), U7.76 (TMS/SWDIO)
/Microcontroller/SWO: J2.13 (SWO), U7.78 (TDO/SWO)
/Microcontroller/TDI: U7.79 (P0_3)
/Microcontroller/VDD_ANA: C41.1, FB1.2, U7.30 (VDD_ANA), U7.31 (VREFH)
/Microcontroller/VDD_SYS: C42.1, U7.55 (VDD_SYS)
/Microcontroller/~ISPMODE: R115.1, U7.82 (ISPMODE_N); also elsewhere on the board
GND: C38.2, C39.2, C40.2, C41.2, C42.2, C43.2, C44.2, C45.2, C48.1, C51.2, C52.2, C53.2, C54.2, C55.2, C56.2, C57.2, C58.2, C59.2, C60.2, D10.1 (K), J2.5 (GND), J2.14 (GND), J2.15 (PAD), J2.16 (PAD), U7.32 (VREFL), U7.33 (VSS_P4), U7.52 (VSS_DCDC), U7.101 (EP), U20.2 (GND), Y2.2 (G), Y2.4 (G); also elsewhere on the board
unnamed: D10.2 (A), R111.1
unnamed: J2.8 (DEBUG-0), TP6.1 (1_1)
unnamed: L3.2, U7.53 (DCDC_LX)
unnamed: R111.2, U7.6 (P1_13)
unnamed: C39.1, U7.10 (XTAL48M), Y2.3
unnamed: C38.1, U7.11 (EXTAL48M), Y2.1
unnamed: U7.4 (CAN0_RXD), U20.4 (RXD)
unnamed: U7.3 (CAN0_TXD), U20.1 (TXD)
VBUSP: J2.1 (VBUSP), J2.2 (VBUSP); also elsewhere on the board
VDD_CORE: C43.1, C53.1, C55.1, L3.1, U7.12 (VDD_CORE), U7.58 (VDD_CORE)

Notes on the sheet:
"MCU"
Note: Disable LDO_CORE in software for more power savings
CAN Transceiver
ALL CAPS ARE 0603, 10%, X5R or better, AEQ, Vw >= 25 V UNLESS OTHERWISE NOTED ALL RESISTORS ARE 0603 1% AEQ UNLESS OTHERWISE NOTED.
- Requires Pullup
OreSat Debug Connector
1.0 - 1.2 V depending on Active mode
VDD_BAT
P0/P1
24 MHz allows LPTMRs to work
0805
RX-TX cross on DEBUG board

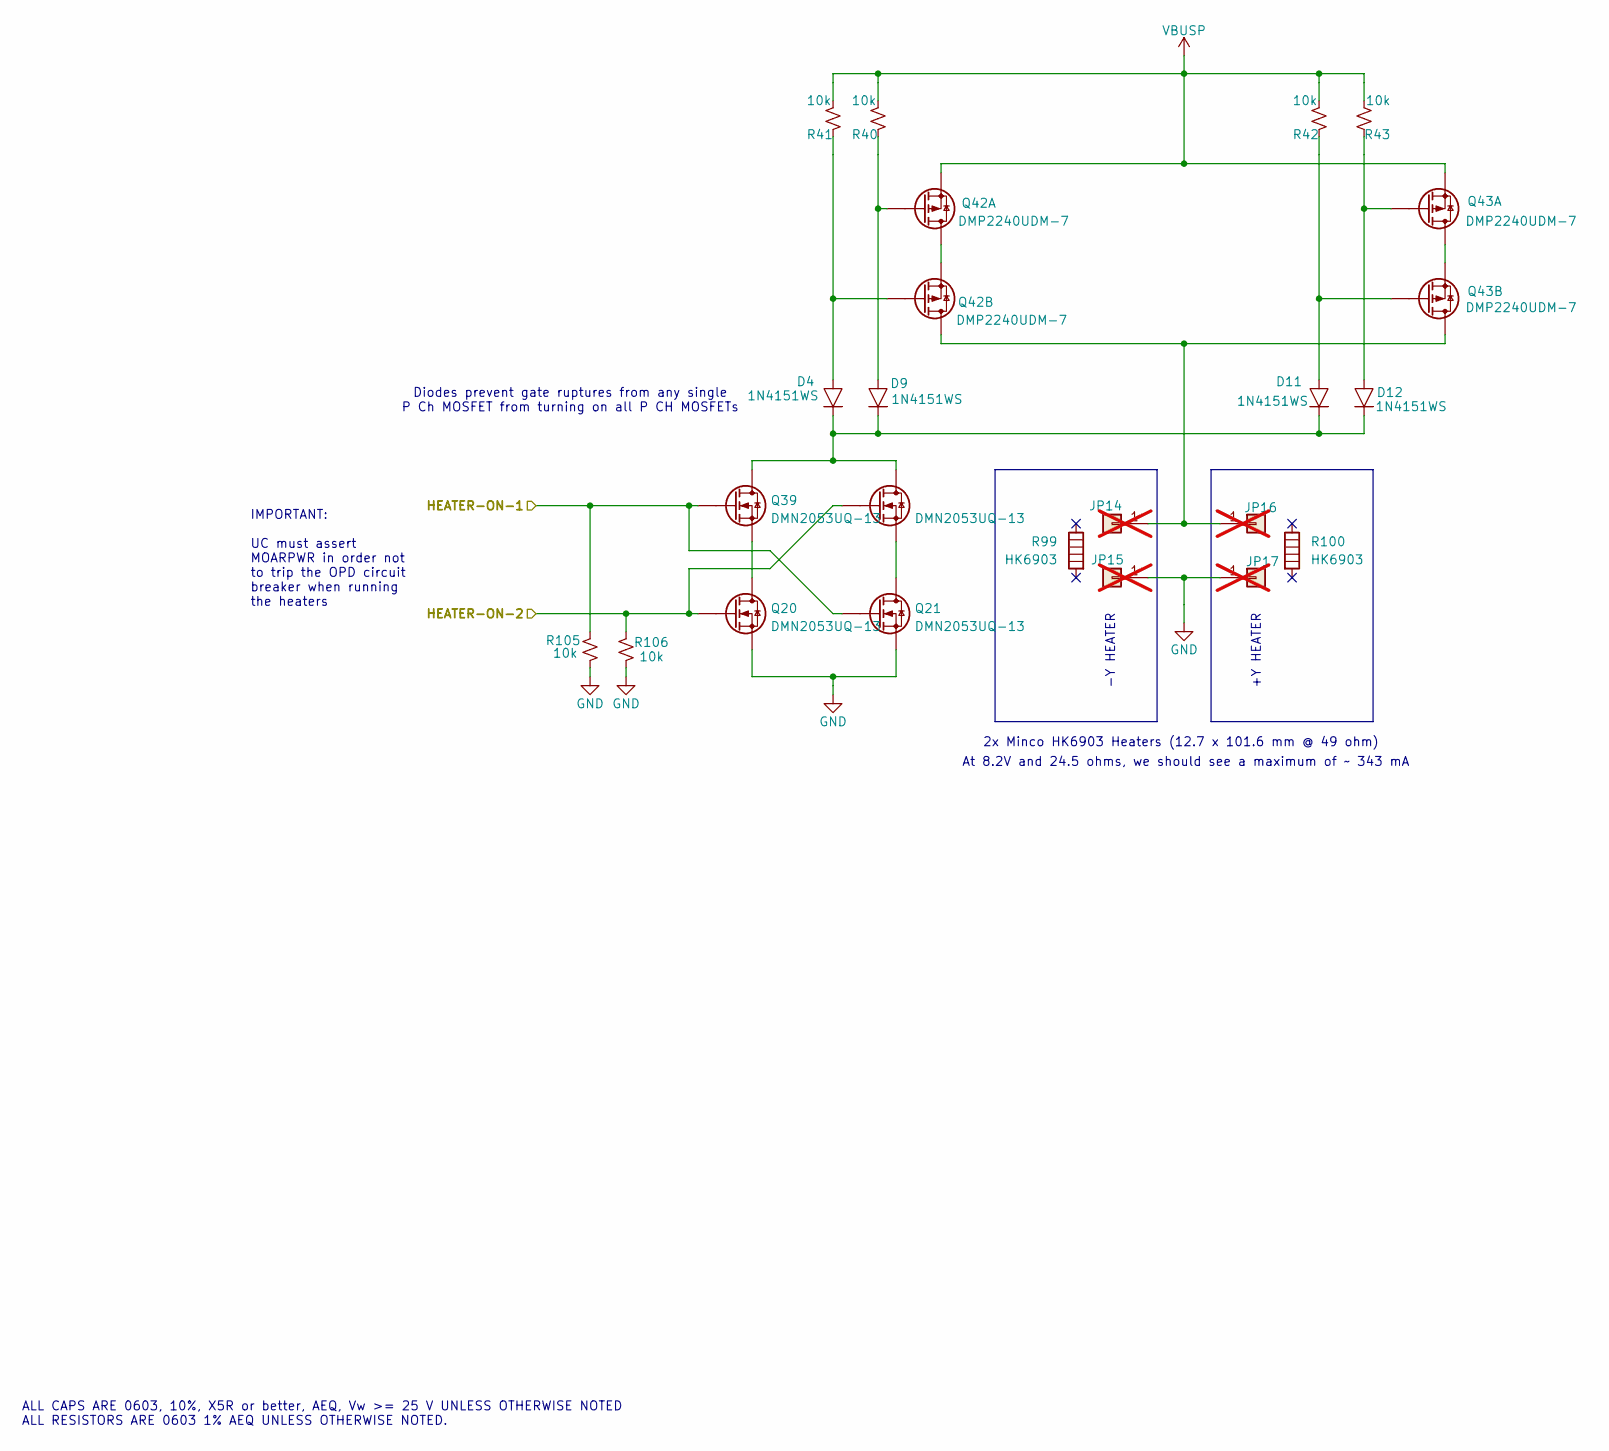
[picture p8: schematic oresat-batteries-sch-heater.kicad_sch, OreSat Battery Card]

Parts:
D4, D9, D11, D12: 1N4151WS; D_SOD-323; MPN 1N4151WS-E3-08
JP14, JP15, JP16, JP17: PINHD-1X1; PinHeader_1x01_P2.54mm_Vertical; MPN N/A; not fitted
Q20, Q21, Q38, Q39: DMN2053UQ-13; SOT-23; MPN DMN2053UQ-13
Q42, Q43: DMP2240UDM-7; SOT-23-6; MPN DMP2240UDM-7
R40, R41, R42, R43, R105, R106: 10k; 0603-C-NOSILK; MPN RMCF0603FT10K0
R99, R100: HK6903; MPN HK6903

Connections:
/Heaters/HEATER-ON-1: Q21.1 (G), Q39.1 (G), R105.2; also elsewhere on the board
/Heaters/HEATER-ON-2: Q20.1 (G), Q38.1 (G), R106.2; also elsewhere on the board
GND: JP15.1 (Pin_1_1), JP17.1 (Pin_1_1), Q20.2 (S), Q21.2 (S), R105.1, R106.1; also elsewhere on the board
unnamed: JP14.1 (Pin_1_1), JP16.1 (Pin_1_1), Q42.4 (D), Q43.4 (D)
unnamed: Q20.3 (D), Q39.2 (S)
unnamed: Q21.3 (D), Q38.2 (S)
unnamed: D4.1, D9.1, D11.1, D12.1, Q38.3 (D), Q39.3 (D)
unnamed: Q42.2 (S), Q42.6 (D)
unnamed: D9.2, Q42.1 (G), R40.1
unnamed: D4.2, Q42.3 (G), R41.1
unnamed: Q43.2 (S), Q43.6 (D)
unnamed: D12.2, Q43.1 (G), R43.1
unnamed: D11.2, Q43.3 (G), R42.1
VBUSP: Q42.5 (S), Q43.5 (S), R40.2, R41.2, R42.2, R43.2; also elsewhere on the board

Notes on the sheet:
IMPORTANT: UC must assert MOARPWR in order not to trip the OPD circuit breaker when running the heaters
2x Minco HK6903 Heaters (12.7 x 101.6 mm @ 49 ohm)
At 8.2V and 24.5 ohms, we should see a maximum of ~ 343 mA
+Y HEATER
Diodes prevent gate ruptures from any single P Ch MOSFET from turning on all P CH MOSFETs
-Y HEATER
ALL CAPS ARE 0603, 10%, X5R or better, AEQ, Vw >= 25 V UNLESS OTHERWISE NOTED ALL RESISTORS ARE 0603 1% AEQ UNLESS OTHERWISE NOTED.

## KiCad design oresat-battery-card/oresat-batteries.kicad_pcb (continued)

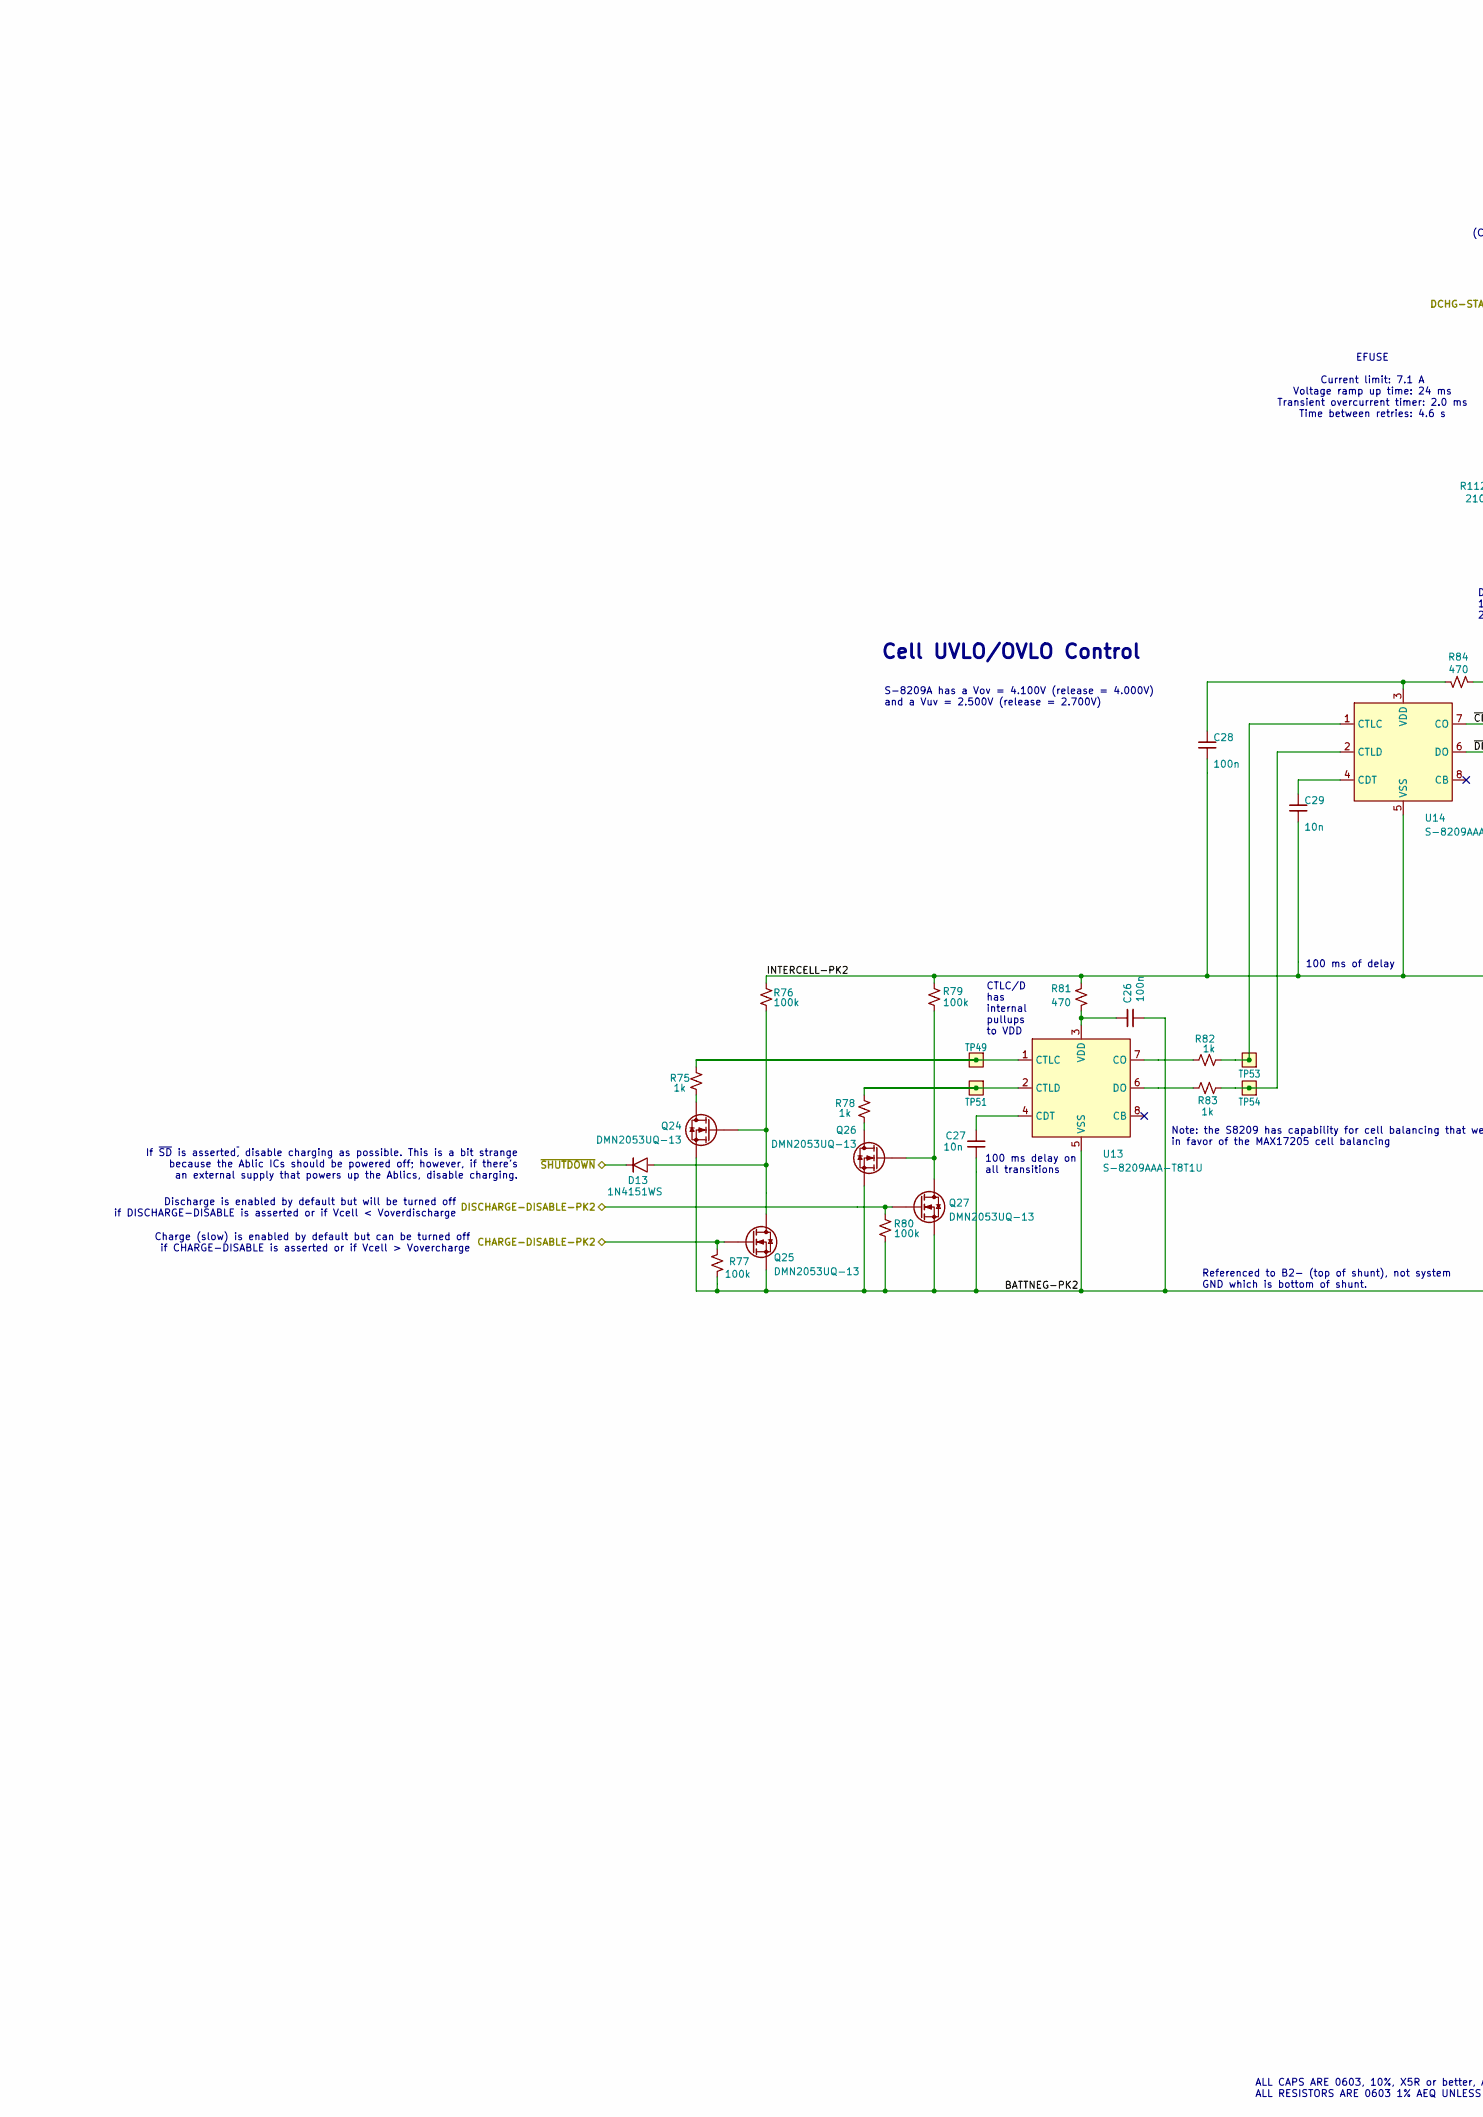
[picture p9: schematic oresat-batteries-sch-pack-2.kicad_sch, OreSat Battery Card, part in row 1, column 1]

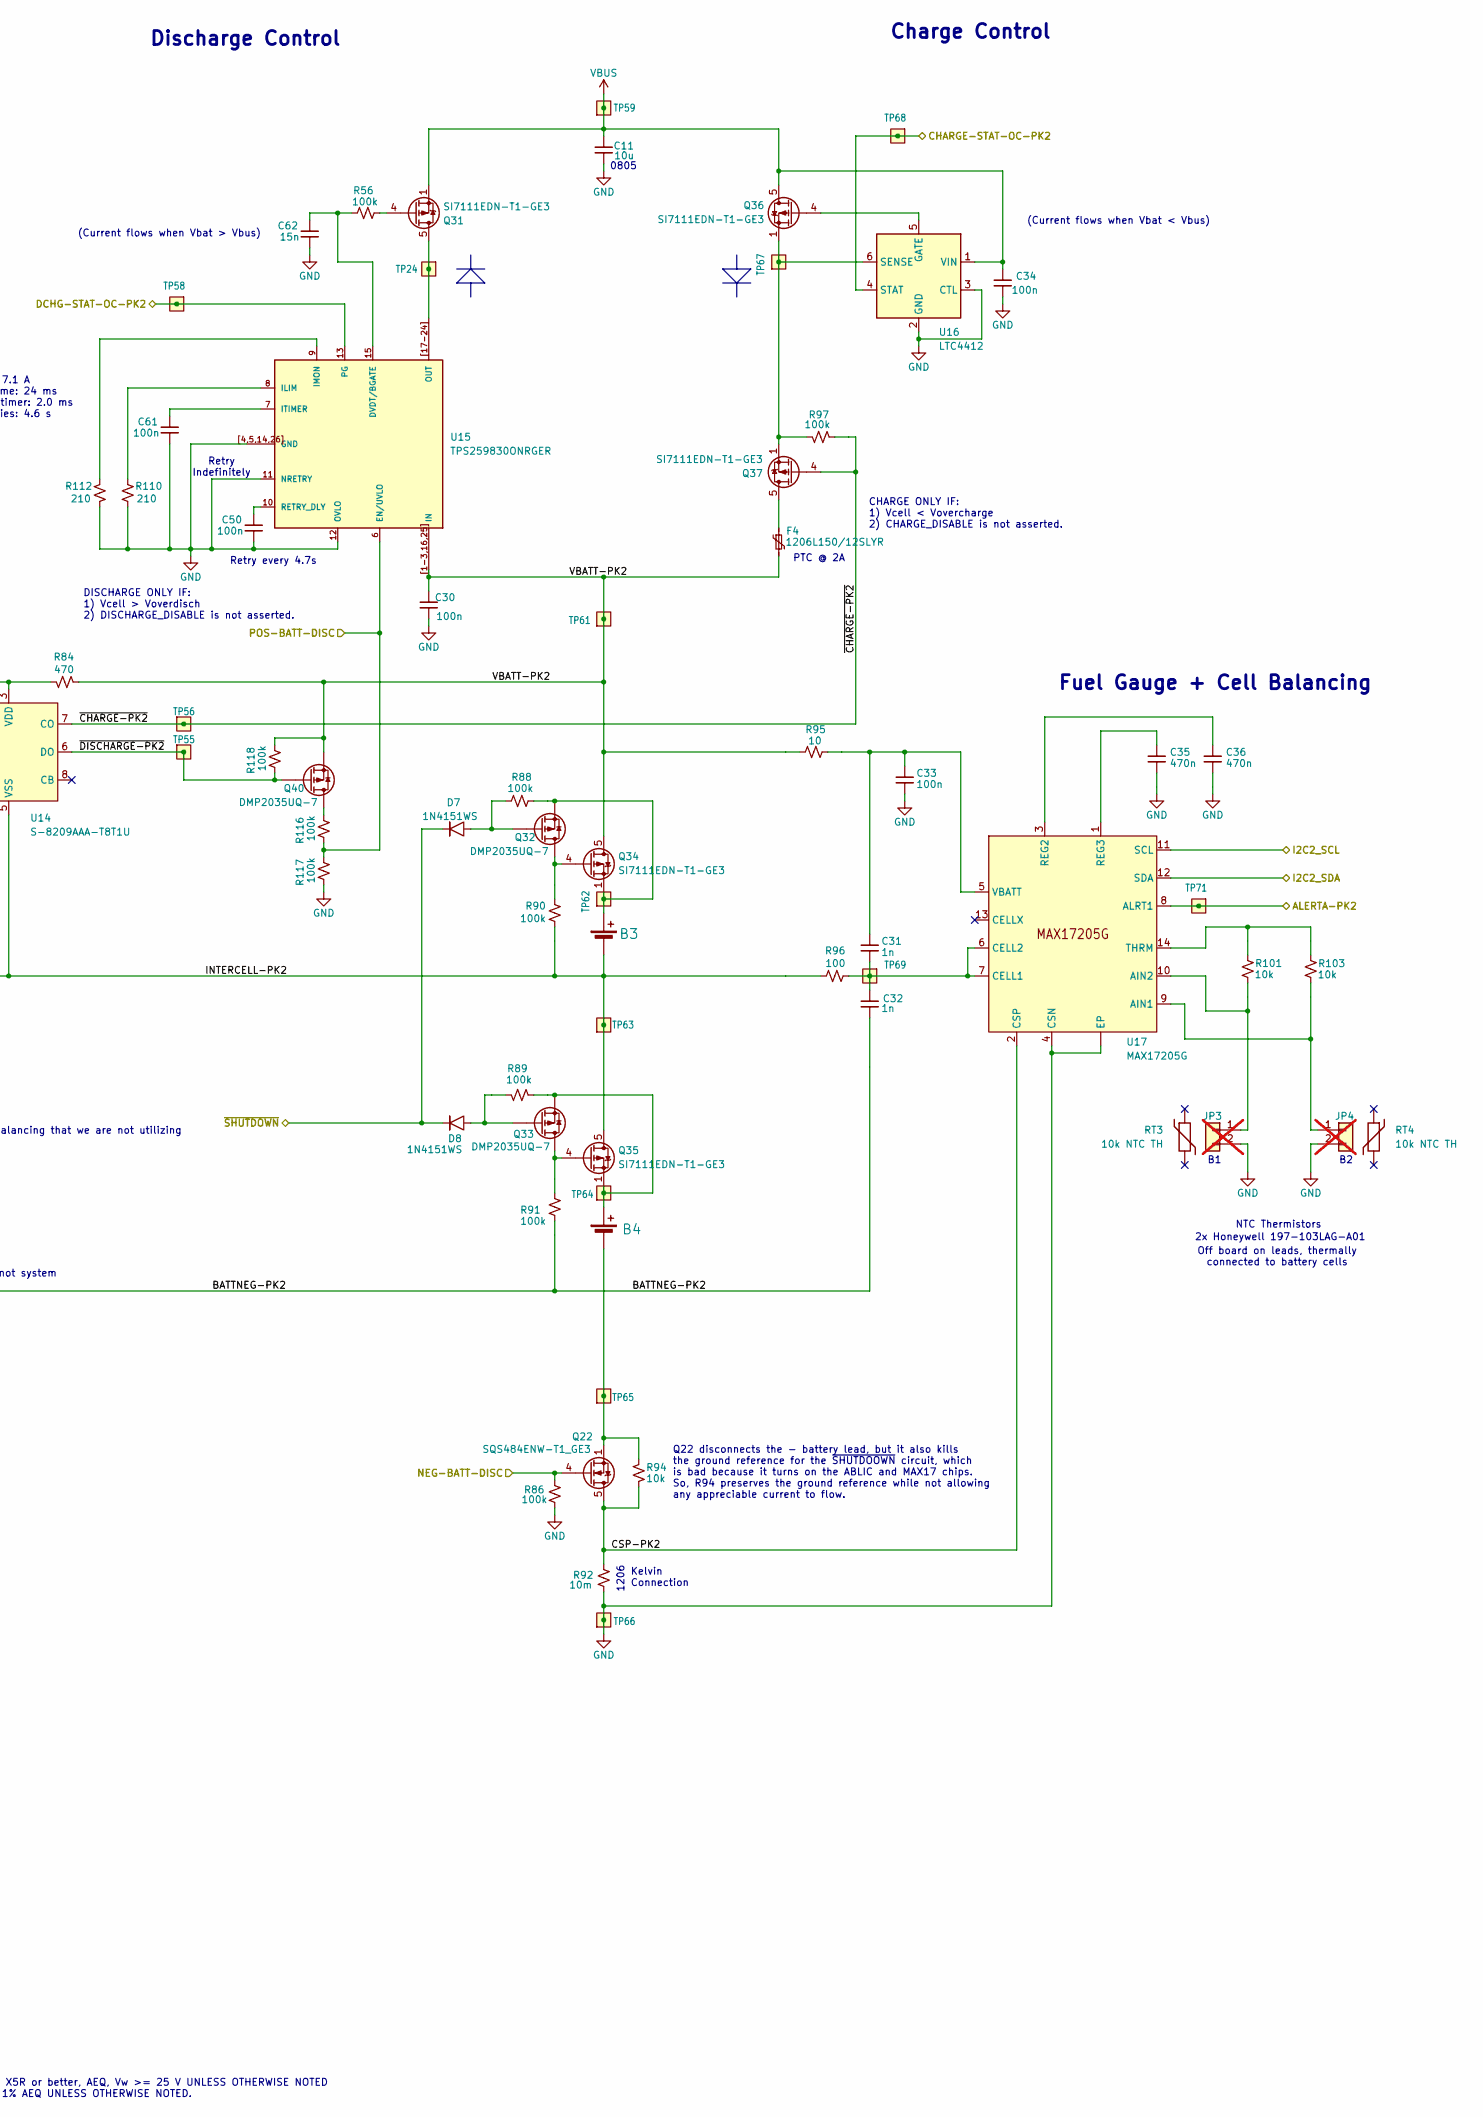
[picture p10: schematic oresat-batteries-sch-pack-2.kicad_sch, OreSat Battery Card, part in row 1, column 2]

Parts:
B3, B4: Tenergy 30005; 18650; MPN MH48285
C11: 10u; 0805-C-NOSILK; MPN GRT21BC71E106KE13K
C26, C28, C30, C33, C34, C50, C61: 100n; 0603-C-NOSILK; MPN C0603C104K5RACAUTO
C27, C29: 10n; 0603-C-NOSILK; MPN C0603C103J5RACAUTO
C31, C32: 1n; 0603-C-NOSILK; MPN C0603C102J5RACAUTO
C35, C36: 470n; 0603-C-NOSILK; MPN C0603C473K5RACAUTO
C62: 15n; 0603-C-NOSILK; MPN C0603C104K5RACAUTO
D7, D8, D13: 1N4151WS; D_SOD-323; MPN 1N4151WS-E3-08
F4: 1206L150/12SLYR; 1206-C; MPN F5765CT-ND
JP3, JP4: PINHD-1X2; PinHeader_1x02_P2.54mm_Vertical; MPN N/A; not fitted
Q22: SQS484ENW-T1_GE3; Vishay_PowerPAK_1212-8_Single; MPN SQS484ENW-T1_GE3
Q24, Q25, Q26, Q27: DMN2053UQ-13; SOT-23; MPN DMN2053UQ-13
Q31, Q34, Q35, Q36, Q37: SI7111EDN-T1-GE3; Vishay_PowerPAK_1212-8_Single; MPN SI7111EDN-T1-GE3
Q32, Q33, Q40: DMP2035UQ-7; SOT-23; MPN DMP2035UQ-7
R56, R76, R77, R79, R80, R86, R88, R89, R90, R91, R97, R116, R117, R118: 100k; 0603-C-NOSILK; MPN RMCF0603FT100K
R75, R78, R82, R83: 1k; 0603-C-NOSILK; MPN RMCF0603FT1K00
R81, R84: 470; 0603-C-NOSILK; MPN RMCF0603FT470R
R92: 10m; 1206-C; MPN CSR1206-0R01F1
R94, R101, R103: 10k; 0603-C-NOSILK; MPN RMCF0603FT10K0
R95: 10; 0603-C-NOSILK; MPN RMCF0603FT10R0
R96: 100; 0603-C-NOSILK; MPN RMCF0603FT100R
R110, R112: 210; 0603-C-NOSILK; MPN RMCF0603FT100K
RT3, RT4: 10k NTC TH; MPN 197-103LAG-A01
TP24, TP49, TP51, TP53, TP54, TP55, TP56, TP58, TP59, TP61, TP62, TP63, TP64, TP65, TP66, TP67, TP68, TP69, TP71: TEST-POINT-LARGE-SQUARE; TestPoint-0.75mm-th
U13, U14: S-8209AAA-T8T1U; TSSOP-8_4.4x3mm_P0.65mm; MPN S-8209AAA-T8T1U
U15: TPS259830ONRGER; U-TPS259830LNRGER; MPN TPS259830ONRGER
U16: LTC4412; TSOT-23-6; MPN MAX4211FETE
U17: MAX17205G; TDFN-14-1EP_3x3mm_P0.4mm_EP1.78x2.35mm_ThermalVias; MPN MAX17205G

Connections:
/Battery Pack 2 (TOP)/ALERTA-PK2: TP71.1 (1_1), U17.8 (ALRT1); also elsewhere on the board
/Battery Pack 2 (TOP)/BATTNEG-PK2: C26.2, C27.2, C32.2, Q24.2 (S), Q25.2 (S), Q26.2 (S), Q27.2 (S), R77.1, R80.1, R91.2, U13.5 (VSS)
/Battery Pack 2 (TOP)/CHARGE-DISABLE-PK2: Q25.1 (G), R77.2; also elsewhere on the board
/Battery Pack 2 (TOP)/CHARGE-STAT-OC-PK2: TP68.1 (1_1), U16.4 (STAT); also elsewhere on the board
/Battery Pack 2 (TOP)/CSP-PK2: Q22.5 (D), R92.1, R94.1, U17.2 (CSP)
/Battery Pack 2 (TOP)/DCHG-STAT-OC-PK2: TP58.1 (1_1), U15.13 (PG); also elsewhere on the board
/Battery Pack 2 (TOP)/DISCHARGE-DISABLE-PK2: Q27.1 (G), R80.2; also elsewhere on the board
/Battery Pack 2 (TOP)/I2C2_SCL: U17.11 (SCL); also elsewhere on the board
/Battery Pack 2 (TOP)/I2C2_SDA: U17.12 (SDA); also elsewhere on the board
/Battery Pack 2 (TOP)/INTERCELL-PK2: B3.2 (-), C28.2, C29.2, Q35.5 (D), R76.2, R79.1, R81.2, R90.2, R96.1, TP63.1 (1_1), U14.5 (VSS)
/Battery Pack 2 (TOP)/VBATT-PK2: C30.1, F4.2, Q34.5 (D), Q40.2 (S), R84.2, R95.2, R118.2, TP61.1 (1_1), U15.1 (IN), U15.2 (IN), U15.3 (IN), U15.16 (IN), U15.25 (IN), U15.[1-3,16,25] (IN)
/Battery Pack 2 (TOP)/~CHARGE-PK2: Q37.4 (G), R97.2, TP56.1 (1_1), U14.7 (CO)
/Battery Pack 2 (TOP)/~DISCHARGE-PK2: Q40.1 (G), R118.1, TP55.1 (1_1), U14.6 (DO)
/INH-NEG-BATT_DISC: Q22.4 (G), R86.1; also elsewhere on the board
/INH-POS-BATT-DISC: R116.1, R117.2, U15.6 (EN/UVLO); also elsewhere on the board
/~SHUTDOWN: D7.1, D8.1, D13.1; also elsewhere on the board
GND: C11.2, C30.2, C33.2, C34.2, C35.2, C36.2, C50.2, C61.2, C62.2, JP3.2, JP4.2, R86.2, R92.2, R110.2, R112.2, R117.1, TP66.1 (1_1), U15.4 (GND), U15.5 (GND), U15.11 (NRETRY), U15.12 (OVLO), U15.14 (GND), U15.26 (GND), U15.[4,5,14,26] (GND), U16.2 (GND), U16.3 (CTL), U17.4 (CSN), U17.15 (EP); also elsewhere on the board
unnamed: B3.1 (+), Q32.2 (S), Q34.1 (S), Q34.2 (S), Q34.3 (S), R88.2, TP62.1 (1_1)
unnamed: B4.1 (+), Q33.2 (S), Q35.1 (S), Q35.2 (S), Q35.3 (S), R89.1, TP64.1 (1_1)
unnamed: B4.2 (-), Q22.1 (S), Q22.2 (S), Q22.3 (S), R94.2, TP65.1 (1_1)
unnamed: JP3.1, R101.1, U17.10 (AIN2)
unnamed: JP4.1, R103.1, U17.9 (AIN1)
unnamed: Q24.3 (D), R75.1
unnamed: D13.2, Q24.1 (G), Q25.3 (D), R76.1
unnamed: Q26.3 (D), R78.1
unnamed: Q26.1 (G), Q27.3 (D), R79.2
unnamed: Q31.5 (D), TP24.1 (1_1), U15.17 (OUT), U15.18 (OUT), U15.19 (OUT), U15.20 (OUT), U15.21 (OUT), U15.22 (OUT), U15.23 (OUT), U15.24 (OUT), U15.[17-24] (OUT)
unnamed: Q31.4 (G), R56.2
unnamed: Q32.3 (D), Q34.4 (G), R90.1
unnamed: D7.2, Q32.1 (G), R88.1
unnamed: Q33.3 (D), Q35.4 (G), R91.1
unnamed: D8.2, Q33.1 (G), R89.2
unnamed: Q36.4 (G), U16.5 (GATE)
unnamed: F4.1, Q37.5 (D)
unnamed: Q40.3 (D), R116.2
unnamed: C27.1, U13.4 (CDT)
unnamed: R82.1, U13.7 (CO)
unnamed: R75.2, TP49.1 (1_1), U13.1 (CTLC)
unnamed: R78.2, TP51.1 (1_1), U13.2 (CTLD)
unnamed: R83.1, U13.6 (DO)
unnamed: C26.1, R81.1, U13.3 (VDD)
unnamed: C29.1, U14.4 (CDT)
unnamed: R82.2, TP53.1 (1_1), U14.1 (CTLC)
unnamed: R83.2, TP54.1 (1_1), U14.2 (CTLD)
unnamed: C28.1, R84.1, U14.3 (VDD)
unnamed: C62.1, R56.1, U15.15 (DVDT/BGATE)
unnamed: R110.1, U15.8 (ILIM)
unnamed: R112.1, U15.9 (IMON)
unnamed: C61.1, U15.7 (ITIMER)
unnamed: C50.1, U15.10 (RETRY_DLY)
unnamed: Q36.1 (S), Q36.2 (S), Q36.3 (S), Q37.1 (S), Q37.2 (S), Q37.3 (S), R97.1, TP67.1 (1_1), U16.6 (SENSE)
unnamed: C31.2, C32.1, R96.2, TP69.1 (1_1), U17.6 (CELL2), U17.7 (CELL1)
unnamed: C36.1, U17.3 (REG2)
unnamed: C35.1, U17.1 (REG3)
unnamed: R101.2, R103.2, U17.14 (THRM)
unnamed: C31.1, C33.1, R95.1, U17.5 (VBATT)
VBUS: C11.1, C34.1, Q31.1 (S), Q31.2 (S), Q31.3 (S), Q36.5 (D), TP59.1 (1_1), U16.1 (VIN); also elsewhere on the board

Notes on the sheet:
(Current flows when Vbat < Vbus)
Charge (slow) is enabled by default but can be turned off if CHARGE-DISABLE is asserted or if Vcell > Vovercharge
CTLC/D has internal pullups to VDD
ALL CAPS ARE 0603, 10%, X5R or better, AEQ, Vw >= 25 V UNLESS OTHERWISE NOTED ALL RESISTORS ARE 0603 1% AEQ UNLESS OTHERWISE NOTED.
PTC @ 2A
Kelvin Connection
NTC Thermistors
S-8209A has a Vov = 4.100V (release = 4.000V) and a Vuv = 2.500V (release = 2.700V)
0805
1206
Discharge is enabled by default but will be turned off if DISCHARGE-DISABLE is asserted or if Vcell < Voverdischarge
Q22 disconnects the - battery lead, but it also kills the ground reference for the ~{SHUTDOOWN} circuit, which is bad because it turns on the ABLIC and MAX17 chips. So, R94 preserves the ground reference while not allowing any appreciable current to flow.
Fuel Gauge + Cell Balancing
Off board on leads, thermally connected to battery cells
If ~{SD} is asserted~{,} disable charging as possible. This is a bit strange because the Ablic ICs should be powered off; however, if there's an external supply that powers up the Ablics, disable charging.
EFUSE Current limit: 7.1 A Voltage ramp up time: 24 ms Transient overcurrent timer: 2.0 ms Time between retries: 4.6 s
Cell UVLO/OVLO Control
CHARGE ONLY IF: 1) Vcell < Vovercharge 2) CHARGE_DISABLE is not asserted.
DISCHARGE ONLY IF: 1) Vcell > Voverdisch 2) DISCHARGE_DISABLE is not asserted.
Note: the S8209 has capability for cell balancing that we are not utilizing in favor of the MAX17205 cell balancing
100 ms of delay
Charge Control
(Current flows when Vbat > Vbus)
Discharge Control
Retry Indefinitely
2x Honeywell 197-103LAG-A01
Referenced to B2- (top of shunt), not system GND which is bottom of shunt.
Retry every 4.7s
100 ms delay on all transitions

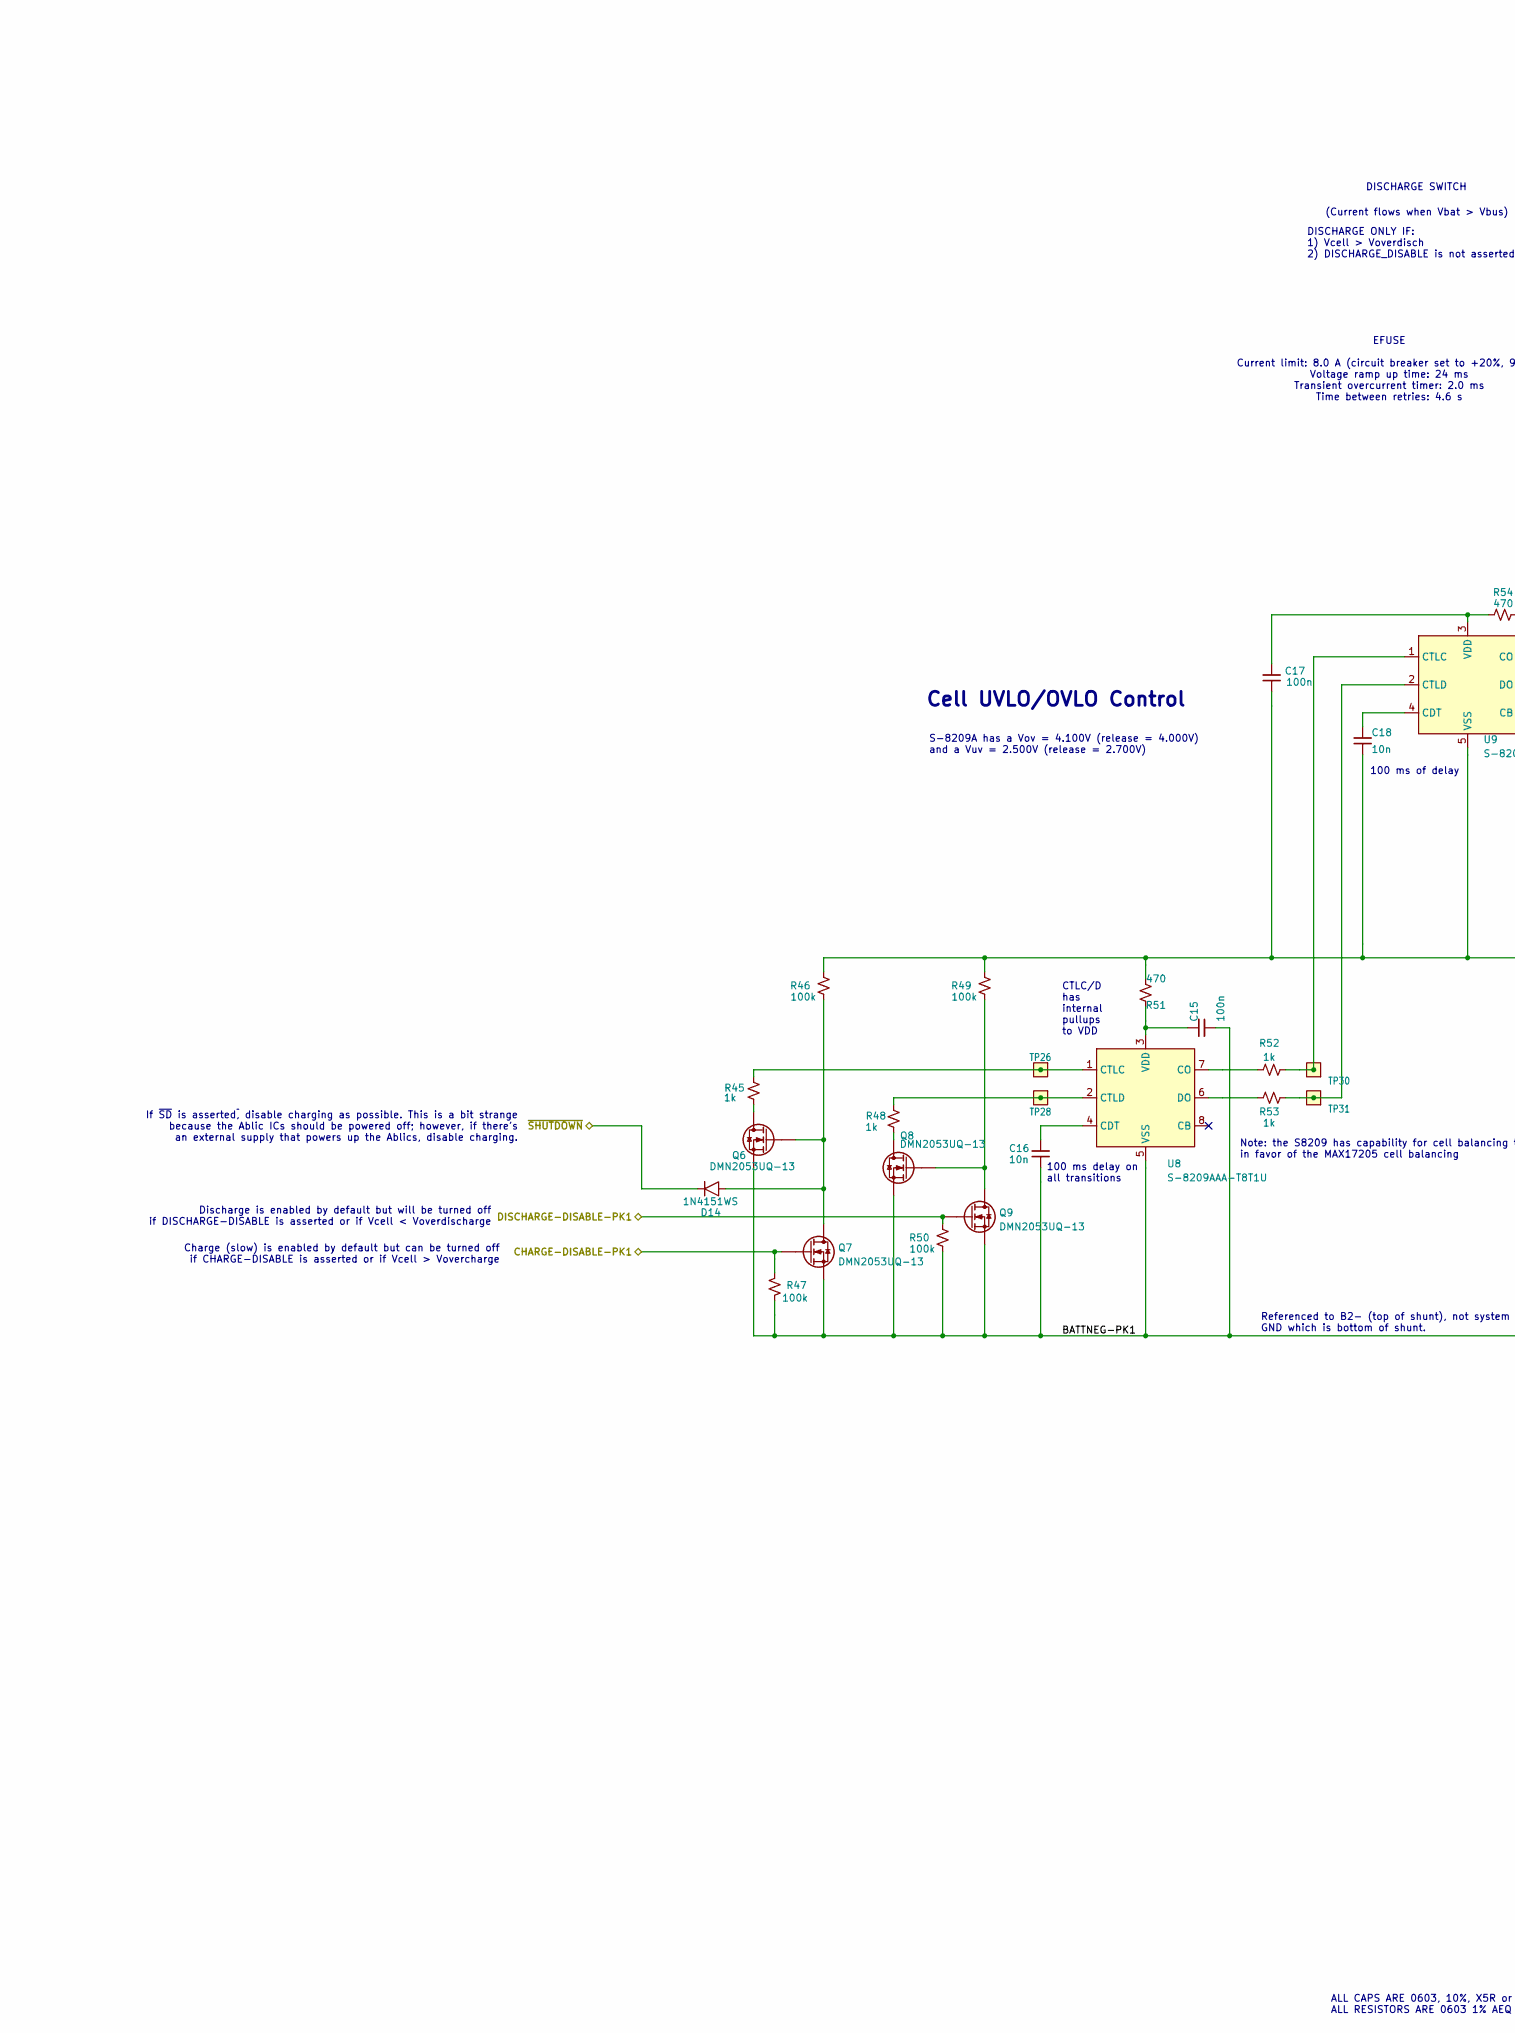
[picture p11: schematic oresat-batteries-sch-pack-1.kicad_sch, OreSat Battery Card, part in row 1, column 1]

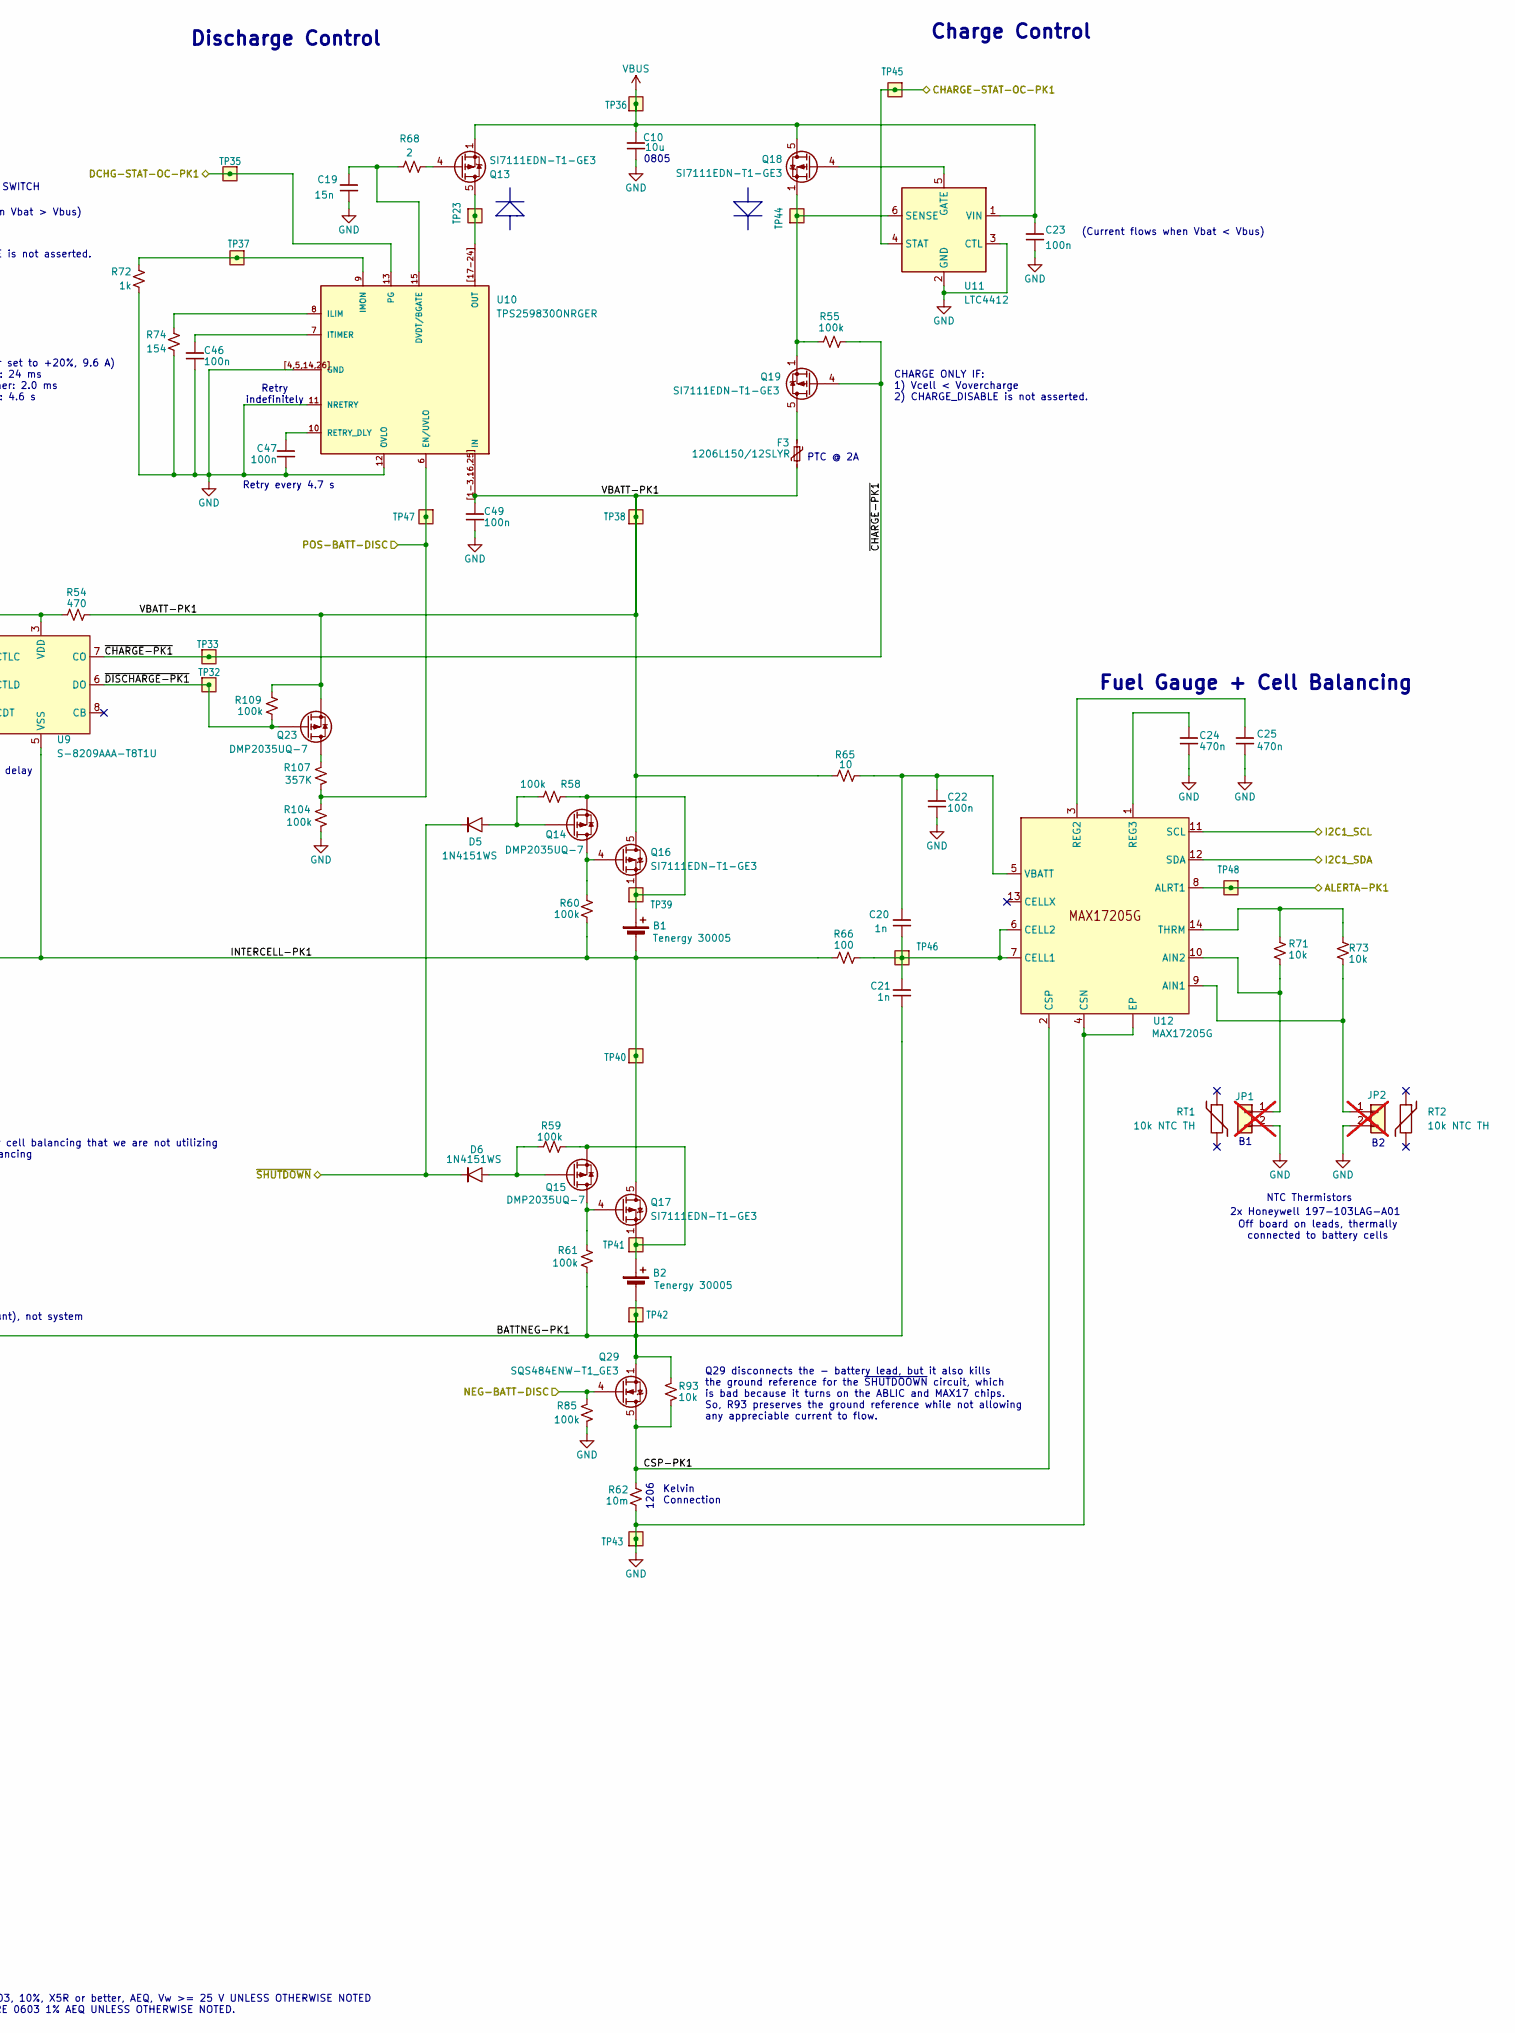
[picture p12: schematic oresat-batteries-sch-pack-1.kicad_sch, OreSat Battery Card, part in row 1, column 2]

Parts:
B1, B2: Tenergy 30005; 18650; MPN MH48285
C10: 10u; 0805-C-NOSILK; MPN GRT21BC71E106KE13K
C15, C17, C22, C23, C46, C47, C49: 100n; 0603-C-NOSILK; MPN C0603C104K5RACAUTO
C16, C18: 10n; 0603-C-NOSILK; MPN C0603C103J5RACAUTO
C19: 15n; 0603-C-NOSILK
C20, C21: 1n; 0603-C-NOSILK; MPN C0603C102J5RACAUTO
C24, C25: 470n; 0603-C-NOSILK; MPN C0603C473K5RACAUTO
D5, D6, D14: 1N4151WS; D_SOD-323; MPN 1N4151WS-E3-08
F3: 1206L150/12SLYR; 1206-C; MPN F5765CT-ND
JP1, JP2: PINHD-1X2; PinHeader_1x02_P2.54mm_Vertical; MPN N/A; not fitted
Q6, Q7, Q8, Q9: DMN2053UQ-13; SOT-23; MPN DMN2053UQ-13
Q13, Q16, Q17, Q18, Q19: SI7111EDN-T1-GE3; Vishay_PowerPAK_1212-8_Single; MPN SI7111EDN-T1-GE3
Q14, Q15, Q23: DMP2035UQ-7; SOT-23; MPN DMP2035UQ-7
Q29: SQS484ENW-T1_GE3; Vishay_PowerPAK_1212-8_Single; MPN SQS484ENW-T1_GE3
R45, R48, R52, R53, R72: 1k; 0603-C-NOSILK; MPN RMCF0603FT1K00
R46, R47, R49, R50, R55, R58, R59, R60, R61, R85, R104, R109: 100k; 0603-C-NOSILK; MPN RMCF0603FT100K
R51, R54: 470; 0603-C-NOSILK; MPN RMCF0603FT470R
R62: 10m; 1206-C; MPN CSR1206-0R01F1
R65: 10; 0603-C-NOSILK; MPN RMCF0603FT10R0
R66: 100; 0603-C-NOSILK; MPN RMCF0603FT100R
R68: 2; 0603-C-NOSILK; MPN RMCF0603FT2R00
R71, R73, R93: 10k; 0603-C-NOSILK; MPN RMCF0603FT10K0
R74: 154; 0603-C-NOSILK; MPN RMCF0603FT154R
R107: 357K; 0603-C-NOSILK; MPN RMCF0603FT357K
RT1, RT2: 10k NTC TH; MPN 197-103LAG-A01
TP23, TP26, TP28, TP30, TP31, TP32, TP33, TP35, TP36, TP37, TP38, TP39, TP40, TP41, TP42, TP43, TP44, TP45, TP46, TP47, TP48: TEST-POINT-LARGE-SQUARE; TestPoint-0.75mm-th
U8, U9: S-8209AAA-T8T1U; TSSOP-8_4.4x3mm_P0.65mm; MPN S-8209AAA-T8T1U
U10: TPS259830ONRGER; U-TPS259830LNRGER; MPN TPS259830ONRGER
U11: LTC4412; TSOT-23-6; MPN MAX4211FETE
U12: MAX17205G; TDFN-14-1EP_3x3mm_P0.4mm_EP1.78x2.35mm_ThermalVias; MPN MAX17205G

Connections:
/Battery Pack 1 (BOTTOM)/ALERTA-PK1: TP48.1 (1_1), U12.8 (ALRT1); also elsewhere on the board
/Battery Pack 1 (BOTTOM)/BATTNEG-PK1: B2.2 (-), C15.2, C16.2, C21.2, Q6.2 (S), Q7.2 (S), Q8.2 (S), Q9.2 (S), Q29.1 (S), Q29.2 (S), Q29.3 (S), R47.1, R50.1, R61.2, R93.2, TP42.1 (1_1), U8.5 (VSS)
/Battery Pack 1 (BOTTOM)/CHARGE-DISABLE-PK1: Q7.1 (G), R47.2; also elsewhere on the board
/Battery Pack 1 (BOTTOM)/CHARGE-STAT-OC-PK1: TP45.1 (1_1), U11.4 (STAT); also elsewhere on the board
/Battery Pack 1 (BOTTOM)/CSP-PK1: Q29.5 (D), R62.1, R93.1, U12.2 (CSP)
/Battery Pack 1 (BOTTOM)/DCHG-STAT-OC-PK1: TP35.1 (1_1), U10.13 (PG); also elsewhere on the board
/Battery Pack 1 (BOTTOM)/DISCHARGE-DISABLE-PK1: Q9.1 (G), R50.2; also elsewhere on the board
/Battery Pack 1 (BOTTOM)/I2C1_SCL: U12.11 (SCL); also elsewhere on the board
/Battery Pack 1 (BOTTOM)/I2C1_SDA: U12.12 (SDA); also elsewhere on the board
/Battery Pack 1 (BOTTOM)/INTERCELL-PK1: B1.2 (-), C17.2, C18.2, Q17.5 (D), R46.2, R49.1, R51.2, R60.2, R66.1, TP40.1 (1_1), U9.5 (VSS)
/Battery Pack 1 (BOTTOM)/VBATT-PK1: C49.1, F3.2, Q16.5 (D), Q23.2 (S), R54.2, R65.2, R109.1, TP38.1 (1_1), U10.1 (IN), U10.2 (IN), U10.3 (IN), U10.16 (IN), U10.25 (IN), U10.[1-3,16,25] (IN)
/Battery Pack 1 (BOTTOM)/~CHARGE-PK1: Q19.4 (G), R55.1, TP33.1 (1_1), U9.7 (CO)
/Battery Pack 1 (BOTTOM)/~DISCHARGE-PK1: Q23.1 (G), R109.2, TP32.1 (1_1), U9.6 (DO)
/INH-NEG-BATT_DISC: Q29.4 (G), R85.1; also elsewhere on the board
/INH-POS-BATT-DISC: R104.2, R107.1, TP47.1 (1_1), U10.6 (EN/UVLO); also elsewhere on the board
/~SHUTDOWN: D5.1, D6.1, D14.1; also elsewhere on the board
GND: C10.2, C19.2, C22.2, C23.2, C24.2, C25.2, C46.2, C47.2, C49.2, JP1.2, JP2.2, R62.2, R72.2, R74.2, R85.2, R104.1, TP43.1 (1_1), U10.4 (GND), U10.5 (GND), U10.11 (NRETRY), U10.12 (OVLO), U10.14 (GND), U10.26 (GND), U10.[4,5,14,26] (GND), U11.2 (GND), U11.3 (CTL), U12.4 (CSN), U12.15 (EP); also elsewhere on the board
unnamed: B1.1 (+), Q14.2 (S), Q16.1 (S), Q16.2 (S), Q16.3 (S), R58.2, TP39.1 (1_1)
unnamed: B2.1 (+), Q15.2 (S), Q17.1 (S), Q17.2 (S), Q17.3 (S), R59.1, TP41.1 (1_1)
unnamed: JP1.1, R71.1, U12.10 (AIN2)
unnamed: JP2.1, R73.1, U12.9 (AIN1)
unnamed: Q6.3 (D), R45.1
unnamed: D14.2, Q6.1 (G), Q7.3 (D), R46.1
unnamed: Q8.3 (D), R48.1
unnamed: Q8.1 (G), Q9.3 (D), R49.2
unnamed: Q13.5 (D), TP23.1 (1_1), U10.17 (OUT), U10.18 (OUT), U10.19 (OUT), U10.20 (OUT), U10.21 (OUT), U10.22 (OUT), U10.23 (OUT), U10.24 (OUT), U10.[17-24] (OUT)
unnamed: Q13.4 (G), R68.1
unnamed: Q14.3 (D), Q16.4 (G), R60.1
unnamed: D5.2, Q14.1 (G), R58.1
unnamed: Q15.3 (D), Q17.4 (G), R61.1
unnamed: D6.2, Q15.1 (G), R59.2
unnamed: Q18.4 (G), U11.5 (GATE)
unnamed: F3.1, Q19.5 (D)
unnamed: Q23.3 (D), R107.2
unnamed: C16.1, U8.4 (CDT)
unnamed: R52.1, U8.7 (CO)
unnamed: R45.2, TP26.1 (1_1), U8.1 (CTLC)
unnamed: R48.2, TP28.1 (1_1), U8.2 (CTLD)
unnamed: R53.1, U8.6 (DO)
unnamed: C15.1, R51.1, U8.3 (VDD)
unnamed: C18.1, U9.4 (CDT)
unnamed: R52.2, TP30.1 (1_1), U9.1 (CTLC)
unnamed: R53.2, TP31.1 (1_1), U9.2 (CTLD)
unnamed: C17.1, R54.1, U9.3 (VDD)
unnamed: C19.1, R68.2, U10.15 (DVDT/BGATE)
unnamed: R74.1, U10.8 (ILIM)
unnamed: R72.1, TP37.1 (1_1), U10.9 (IMON)
unnamed: C46.1, U10.7 (ITIMER)
unnamed: C47.1, U10.10 (RETRY_DLY)
unnamed: Q18.1 (S), Q18.2 (S), Q18.3 (S), Q19.1 (S), Q19.2 (S), Q19.3 (S), R55.2, TP44.1 (1_1), U11.6 (SENSE)
unnamed: C20.2, C21.1, R66.2, TP46.1 (1_1), U12.6 (CELL2), U12.7 (CELL1)
unnamed: C25.1, U12.3 (REG2)
unnamed: C24.1, U12.1 (REG3)
unnamed: R71.2, R73.2, U12.14 (THRM)
unnamed: C20.1, C22.1, R65.1, U12.5 (VBATT)
VBUS: C10.1, C23.1, Q13.1 (S), Q13.2 (S), Q13.3 (S), Q18.5 (D), TP36.1 (1_1), U11.1 (VIN); also elsewhere on the board

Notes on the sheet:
Discharge Control
CHARGE ONLY IF: 1) Vcell < Vovercharge 2) CHARGE_DISABLE is not asserted.
CTLC/D has internal pullups to VDD
Q29 disconnects the - battery lead, but it also kills the ground reference for the ~{SHUTDOOWN} circuit, which is bad because it turns on the ABLIC and MAX17 chips. So, R93 preserves the ground reference while not allowing any appreciable current to flow.
EFUSE Current limit: 8.0 A (circuit breaker set to +20%, 9.6 A) Voltage ramp up time: 24 ms Transient overcurrent timer: 2.0 ms Time between retries: 4.6 s
PTC @ 2A
(Current flows when Vbat > Vbus)
(Current flows when Vbat < Vbus)
Discharge is enabled by default but will be turned off if DISCHARGE-DISABLE is asserted or if Vcell < Voverdischarge
NTC Thermistors
Note: the S8209 has capability for cell balancing that we are not utilizing in favor of the MAX17205 cell balancing
Fuel Gauge + Cell Balancing
Kelvin Connection
Retry every 4.7 s
Charge (slow) is enabled by default but can be turned off if CHARGE-DISABLE is asserted or if Vcell > Vovercharge
S-8209A has a Vov = 4.100V (release = 4.000V) and a Vuv = 2.500V (release = 2.700V)
DISCHARGE SWITCH
Referenced to B2- (top of shunt), not system GND which is bottom of shunt.
Off board on leads, thermally connected to battery cells
If ~{SD} is asserted~{,} disable charging as possible. This is a bit strange because the Ablic ICs should be powered off; however, if there's an external supply that powers up the Ablics, disable charging.
1206
Cell UVLO/OVLO Control
100 ms delay on all transitions
2x Honeywell 197-103LAG-A01
ALL CAPS ARE 0603, 10%, X5R or better, AEQ, Vw >= 25 V UNLESS OTHERWISE NOTED ALL RESISTORS ARE 0603 1% AEQ UNLESS OTHERWISE NOTED.
Retry indefinitely
DISCHARGE ONLY IF: 1) Vcell > Voverdisch 2) DISCHARGE_DISABLE is not asserted.
100 ms of delay
Charge Control
0805

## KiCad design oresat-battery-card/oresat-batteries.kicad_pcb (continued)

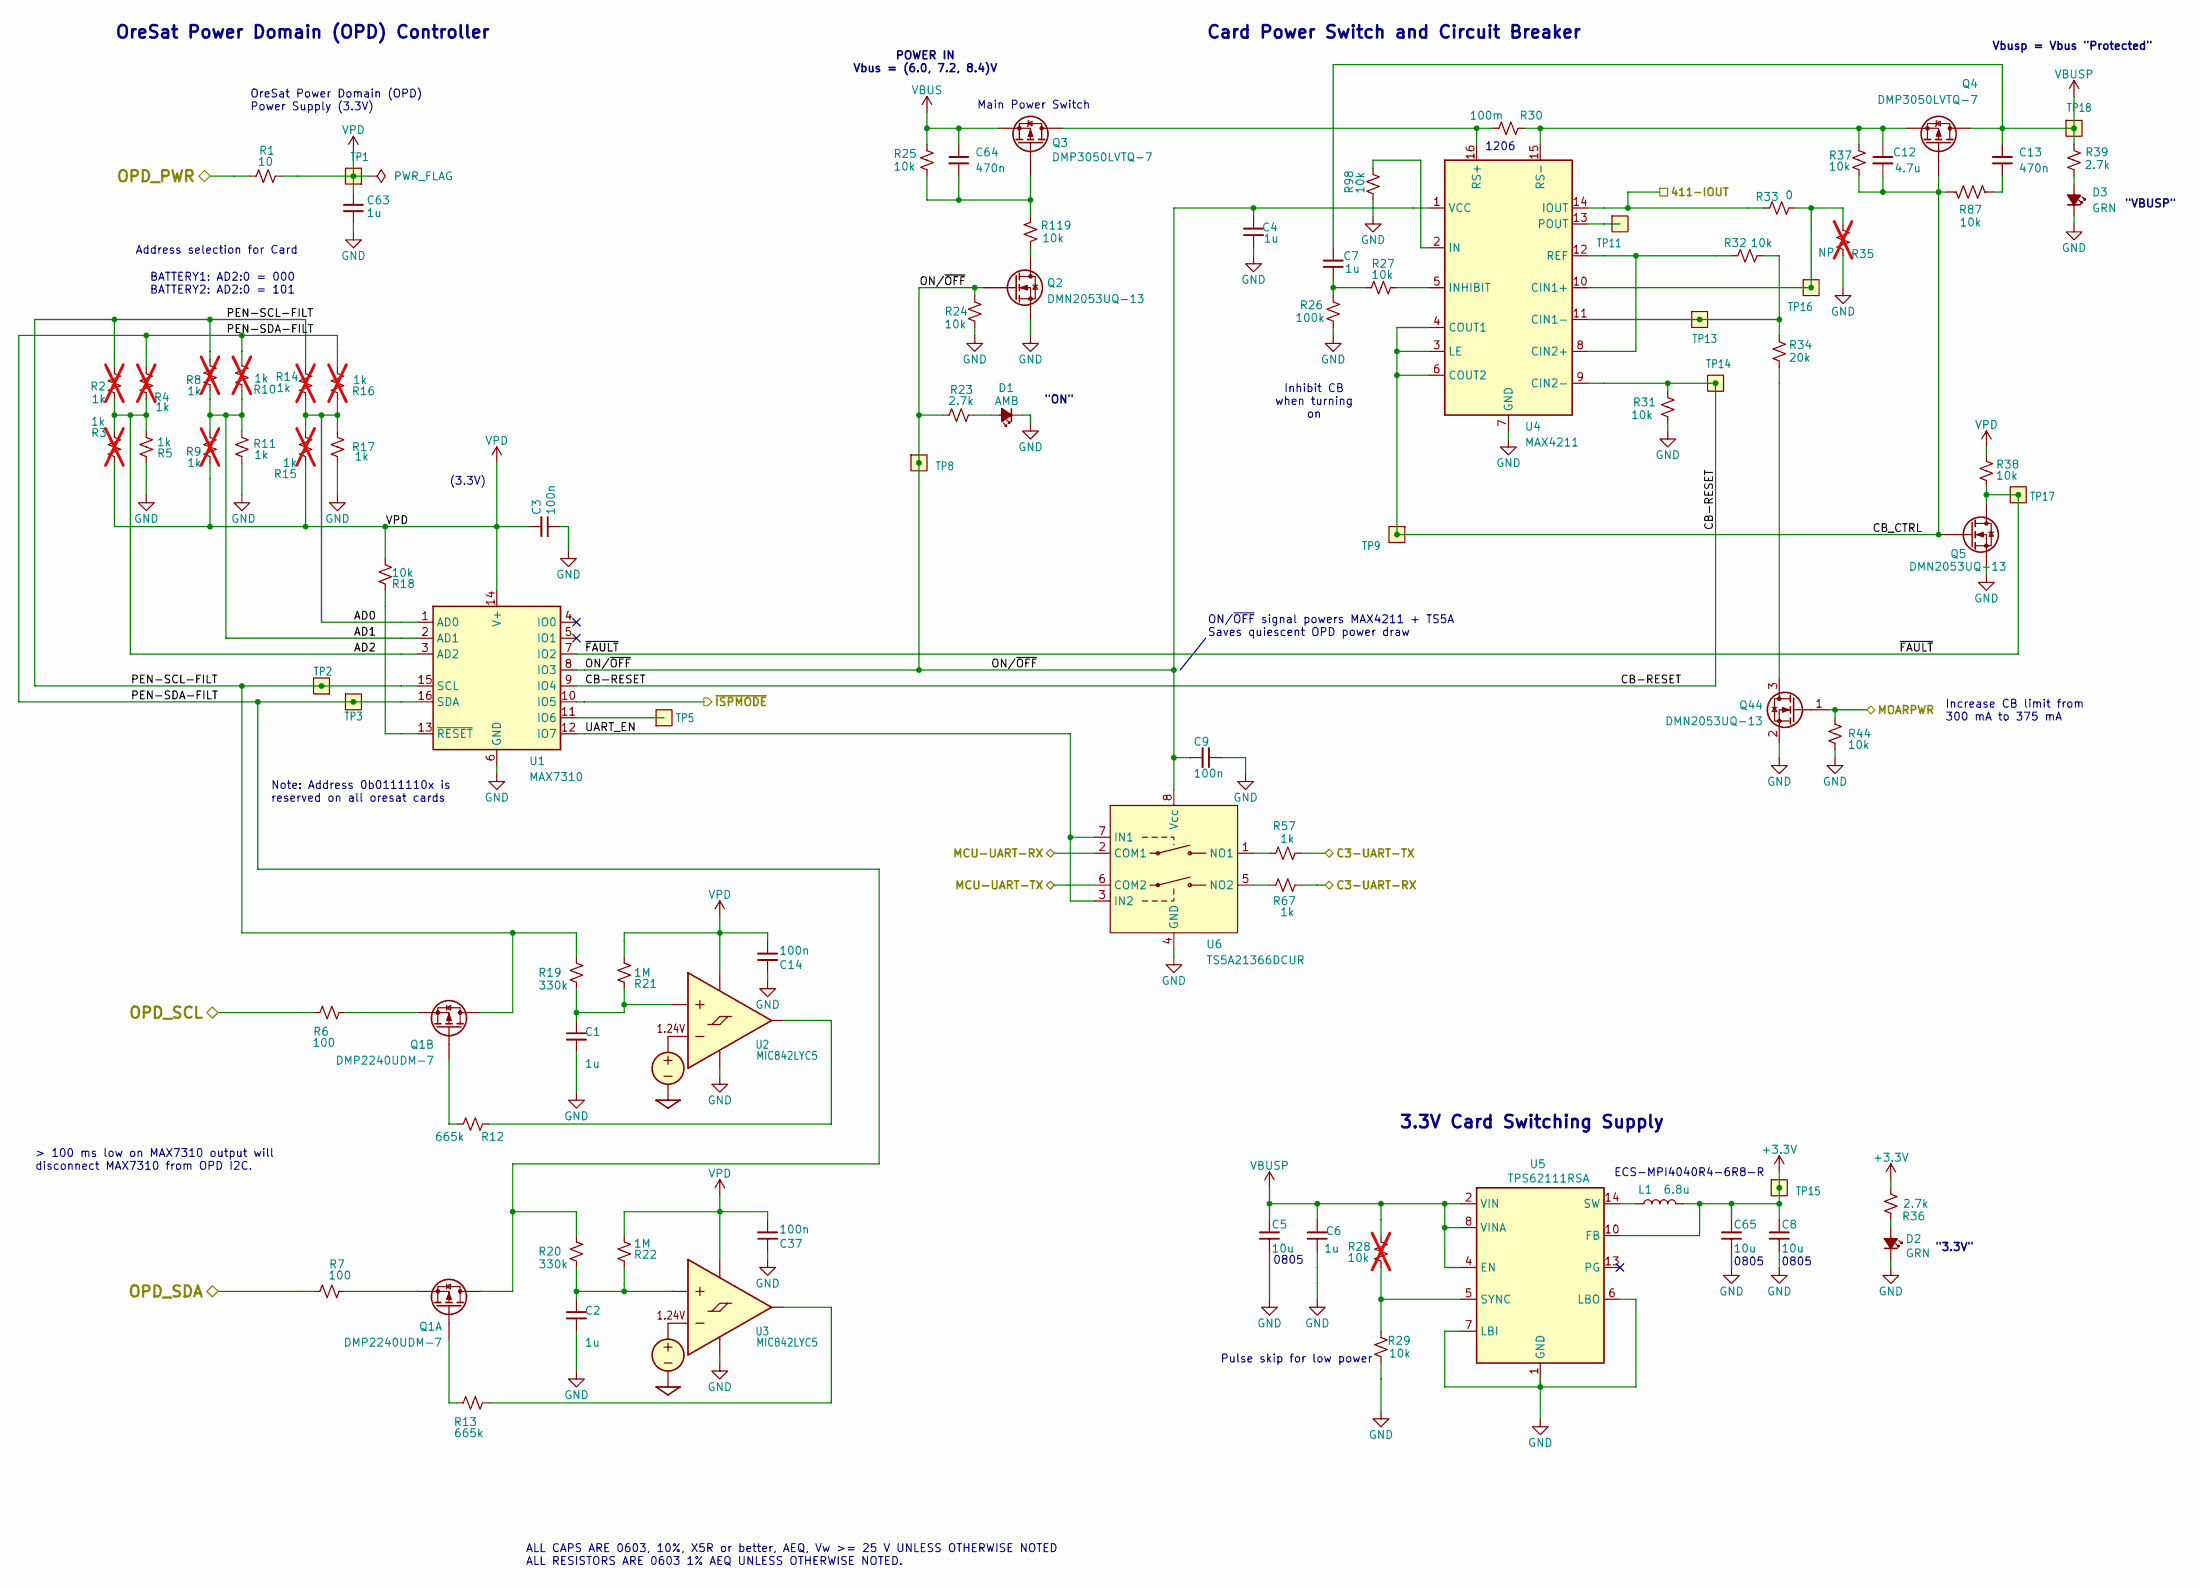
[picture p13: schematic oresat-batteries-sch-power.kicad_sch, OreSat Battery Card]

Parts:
C1, C2, C4, C6, C7, C63: 1u; 0603-C-NOSILK; MPN GRT188R71E105KE13D
C3, C9, C14, C37: 100n; 0603-C-NOSILK; MPN C0603C104K5RACAUTO
C5, C8, C65: 10u; 0805-C-NOSILK; MPN GRT21BC71E106KE13K
C12: 4.7u; 0805-C-NOSILK
C13, C64: 470n; 0603-C-NOSILK; MPN C0603C473K5RACAUTO
D1: AMB; LED_0603_1608Metric; MPN 150060AS75000
D2, D3: GRN; LED_0603_1608Metric; MPN 150060GS75000
L1: 6.8u; L_ECS-MPI4040; MPN ECS-MPI4040R4-6R8-R
Q1: DMP2240UDM-7; SOT-23-6; MPN DMP2240UDM-7
Q2, Q5, Q44: DMN2053UQ-13; SOT-23; MPN DMN2053UQ-13
Q3, Q4: DMP3050LVTQ-7; TSOT-23-6; MPN DMP3050LVTQ-7
R1: 10; 0603-C-NOSILK; MPN RMCF0603FT10R0
R2, R3, R4, R8, R9, R10, R14, R15, R16: 1k; 0603-C-NOSILK; MPN RMCF0603FT1K00; not fitted
R5, R11, R17, R57, R67: 1k; 0603-C-NOSILK; MPN RMCF0603FT1K00
R6, R7: 100; 0603-C-NOSILK; MPN RMCF0603FT100R
R12, R13: 665k; 0603-C-NOSILK; MPN RMCF0603FT665K
R18, R24, R25, R27, R29, R31, R32, R37, R38, R44, R87, R98, R119: 10k; 0603-C-NOSILK; MPN RMCF0603FT10K0
R19, R20: 330k; 0603-C-NOSILK; MPN RMCF0603FT330K
R21, R22: 1M; 0603-C-NOSILK; MPN RMCF0603FT1M00
R23, R36, R39: 2.7k; 0603-C-NOSILK; MPN RMCF0603FT2K70
R26: 100k; 0603-C-NOSILK; MPN RMCF0603FT100K
R28: 10k; 0603-C-NOSILK; MPN RC0603FR-0710KL; not fitted
R30: 100m; 1206-C; MPN CSR1206FKR100
R33: 0; 0603-C-NOSILK; MPN RMCF0603ZT0R00
R34: 20k; 0603-C-NOSILK; MPN RMCF0603FT20K0
R35: NP; 0603-C-NOSILK; MPN RC1005F6653CS; not fitted
TP1, TP2, TP3, TP5, TP8, TP9, TP11, TP13, TP14, TP15, TP16, TP17, TP18: TEST-POINT-LARGE-SQUARE; TestPoint-0.75mm-th
U1: MAX7310; QFN-16-1EP_4x4mm_P0.65mm_EP2.1x2.1mm; MPN MAX7310ATE+
U2, U3: MIC842LYC5; SOT-353_SC-70-5; MPN MIC842LYC5-TR
U4: MAX4211; QFN-16-1EP_4x4mm_P0.65mm_EP2.1x2.1mm; MPN MAX4211FETE
U5: TPS62111RSA; Texas_RSA_VQFN-16-1EP_4x4mm_P0.65mm_EP2.7x2.7mm; MPN TPS62111RSA
U6: TS5A21366DCUR; VSSOP-8_2.3x2mm_P0.5mm; MPN TS5A21366DCUR

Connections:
+3.3V: C8.1, C65.1, L1.2, R36.2, TP15.1 (1_1), U5.10 (FB); also elsewhere on the board
/C3-UART-RX: R67.2; also elsewhere on the board
/C3-UART-TX: R57.2; also elsewhere on the board
/Microcontroller/411-IOUT: R33.2, U4.14 (IOUT); also elsewhere on the board
/Microcontroller/MCU-UART-RX: U6.2 (COM1); also elsewhere on the board
/Microcontroller/MCU-UART-TX: U6.6 (COM2); also elsewhere on the board
/Microcontroller/MOARPWR: Q44.1 (G), R44.2; also elsewhere on the board
/Microcontroller/~ISPMODE: U1.10 (IO5); also elsewhere on the board
/OPD_PWR: R1.1; also elsewhere on the board
/OPD_SCL: R6.1; also elsewhere on the board
/OPD_SDA: R7.1; also elsewhere on the board
/OreSat Power Domain (OPD)/AD0: R14.2, R15.1, R16.1, R17.2, U1.1 (AD0)
/OreSat Power Domain (OPD)/AD1: R8.2, R9.1, R10.1, R11.2, U1.2 (AD1)
/OreSat Power Domain (OPD)/AD2: R2.2, R3.2, R4.1, R5.2, U1.3 (AD2)
/OreSat Power Domain (OPD)/CB-RESET: R31.2, TP14.1 (1_1), U1.9 (IO4), U4.9 (CIN2-)
/OreSat Power Domain (OPD)/CB_CTRL: C12.2, Q4.3 (G), Q5.1 (G), R37.1, R87.2, TP9.1 (1_1), U4.3 (LE), U4.4 (COUT1), U4.6 (COUT2)
/OreSat Power Domain (OPD)/ON/~OFF: C4.1, C9.2, Q2.1 (G), R23.2, R24.2, TP8.1 (1_1), U1.8 (IO3), U4.1 (VCC), U6.8 (Vcc)
/OreSat Power Domain (OPD)/PEN-SCL-FILT: Q1.4 (D), R2.1, R8.1, R14.1, R19.2, TP2.1 (1_1), U1.15 (SCL)
/OreSat Power Domain (OPD)/PEN-SDA-FILT: Q1.6 (D), R4.2, R10.2, R16.2, R20.2, TP3.1 (1_1), U1.16 (SDA)
/OreSat Power Domain (OPD)/UART_EN: U1.12 (IO7), U6.3 (IN2), U6.7 (IN1)
/OreSat Power Domain (OPD)/~FAULT: Q5.3 (D), R38.1, TP17.1 (1_1), U1.7 (IO2)
GND: C1.2, C2.2, C3.1, C4.2, C5.2, C6.2, C8.2, C9.1, C14.2, C37.2, C63.2, C65.2, D1.1 (K), D2.1 (K), D3.1 (K), Q2.2 (S), Q5.2 (S), Q44.2 (S), R5.1, R11.1, R17.1, R24.1, R26.1, R29.1, R31.1, R35.1, R44.1, R98.2, U1.6 (GND), U1.17 (GND), U2.2 (GND), U3.2 (GND), U4.7 (GND), U4.17 (GND), U5.1 (GND), U5.6 (LBO), U5.7 (LBI), U5.9 (GND), U5.11 (GND), U5.12 (GND), U5.16 (GND), U5.17 (GND), U6.4 (GND); also elsewhere on the board
unnamed: C7.1, R26.2, R27.2
unnamed: C13.2, R87.1
unnamed: D1.2 (A), R23.1
unnamed: D2.2 (A), R36.1
unnamed: D3.2 (A), R39.1
unnamed: L1.1, U5.14 (SW), U5.15 (SW)
unnamed: Q1.1 (G), R13.2
unnamed: Q1.5 (S), R7.2
unnamed: Q1.3 (G), R12.2
unnamed: Q1.2 (S), R6.2
unnamed: Q2.3 (D), R119.1
unnamed: C64.2, Q3.3 (G), R25.1, R119.2
unnamed: C12.1, Q4.4 (S), R30.2, R37.2, U4.15 (RS-)
unnamed: Q44.3 (D), R34.1
unnamed: TP5.1 (1_1), U1.11 (IO6)
unnamed: R18.1, U1.13 (~RESET)
unnamed: C1.1, R19.1, R21.1, U2.1 (INP)
unnamed: R12.1, U2.4 (OUT)
unnamed: C2.1, R20.1, R22.1, U3.1 (INP)
unnamed: R13.1, U3.4 (OUT)
unnamed: R33.1, R35.2, TP16.1 (1_1), U4.10 (CIN1+)
unnamed: R32.1, R34.2, TP13.1 (1_1), U4.11 (CIN1-)
unnamed: R32.2, U4.8 (CIN2+), U4.12 (REF)
unnamed: R98.1, U4.2 (IN)
unnamed: R27.1, U4.5 (INHIBIT)
unnamed: TP11.1 (1_1), U4.13 (POUT)
unnamed: Q3.1 (D), Q3.2 (D), Q3.5 (D), Q3.6 (D), R30.1, U4.16 (RS+)
unnamed: R28.1, R29.2, U5.5 (SYNC)
unnamed: R57.1, U6.1 (NO1)
unnamed: R67.1, U6.5 (NO2)
VBUS: C64.1, Q3.4 (S), R25.2; also elsewhere on the board
VBUSP: C5.1, C6.1, C7.2, C13.1, Q4.1 (D), Q4.2 (D), Q4.5 (D), Q4.6 (D), R28.2, R39.2, TP18.1 (1_1), U5.2 (VIN), U5.3 (VIN), U5.4 (EN), U5.8 (VINA); also elsewhere on the board
VPD: C3.2, C14.1, C37.1, C63.1, R1.2, R3.1, R9.2, R15.2, R18.2, R21.2, R22.2, R38.2, TP1.1 (1_1), U1.14 (V+), U2.5 (VDD), U3.5 (VDD)

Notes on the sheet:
Card Power Switch and Circuit Breaker
"3.3V"
0805
3.3V Card Switching Supply
(3.3V)
Main Power Switch
"ON"
OreSat Power Domain (OPD) Power Supply (3.3V)
Increase CB limit from 300 mA to 375 mA
Address selection for Card
Pulse skip for low power
Note: Address 0b0111110x is reserved on all oresat cards
ALL CAPS ARE 0603, 10%, X5R or better, AEQ, Vw >= 25 V UNLESS OTHERWISE NOTED ALL RESISTORS ARE 0603 1% AEQ UNLESS OTHERWISE NOTED.
> 100 ms low on MAX7310 output will disconnect MAX7310 from OPD I2C.
ECS-MPI4040R4-6R8-R
Inhibit CB when turning on
BATTERY1: AD2:0 = 000 BATTERY2: AD2:0 = 101
POWER IN Vbus = (6.0, 7.2, 8.4)V
Vbusp = Vbus "Protected"
OreSat Power Domain (OPD) Controller
1206
"VBUSP"
ON/~{OFF} signal powers MAX4211 + TS5A Saves quiescent OPD power draw

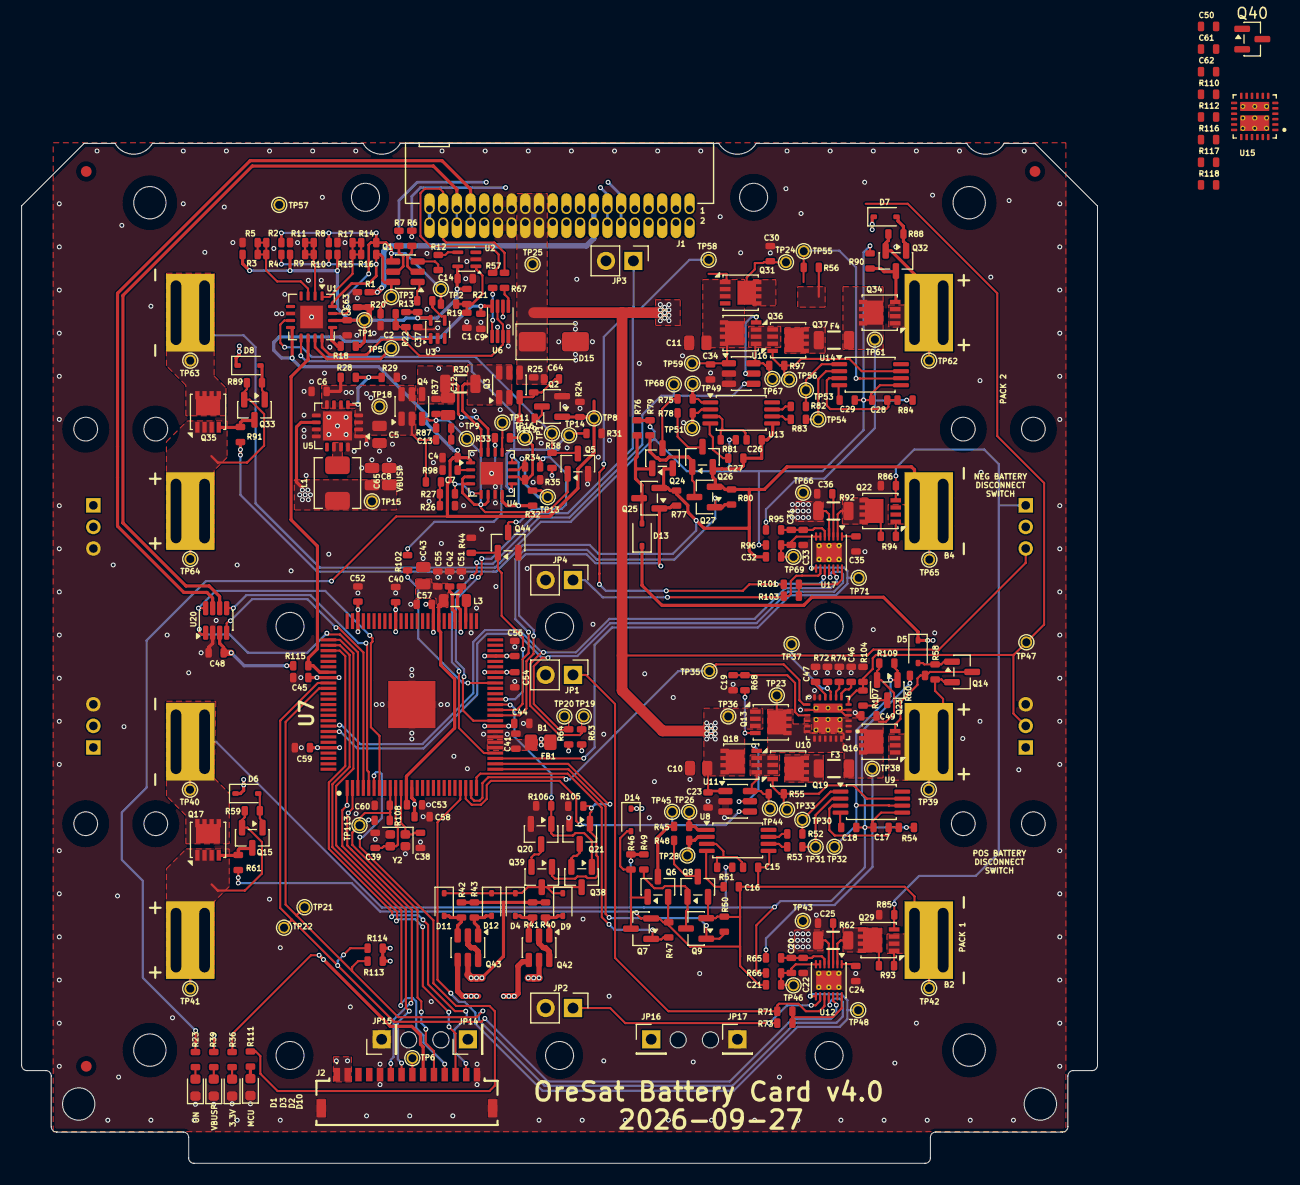
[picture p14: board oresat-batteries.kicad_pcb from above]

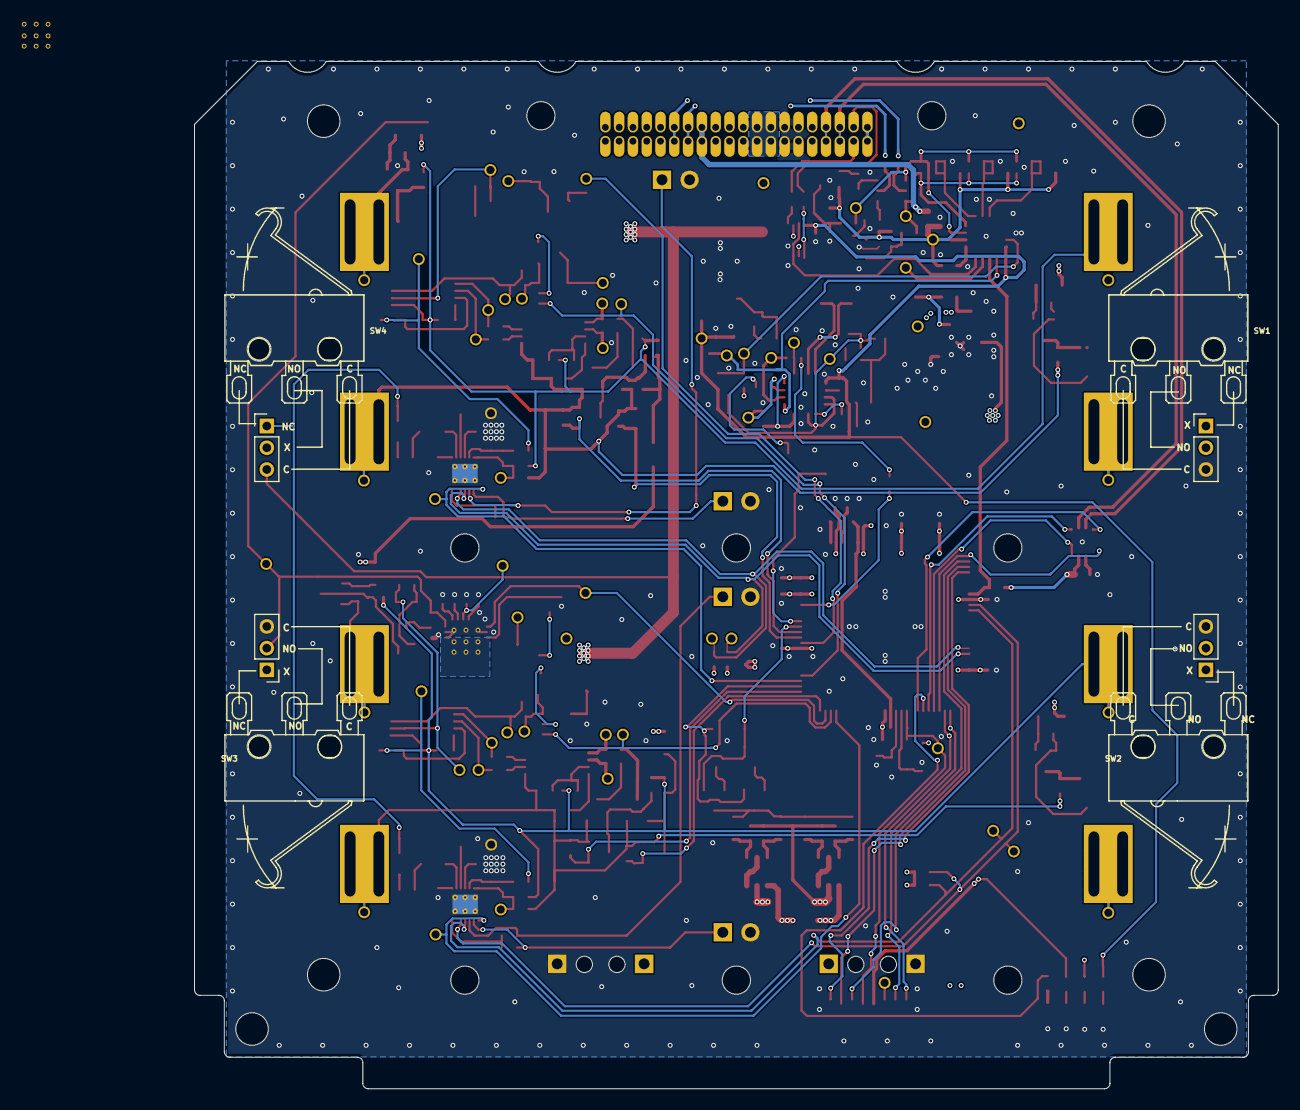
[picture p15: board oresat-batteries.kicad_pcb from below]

Board: 4 copper layers, 99.8 x 94.6 mm, 340 parts (4 on the bottom side), 193 nets.

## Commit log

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2017-04-18 Swapped fuel gauge for ti BQ27500
    [oresatt-batteries.brd, oresatt-batteries.sch]
2017-04-25 Replaced BQ27500 with STC300lST
    [oresatt-batteries.brd, oresatt-batteries.sch]
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2017-06-23 Added, resistive heater, half of shutdown circuitry, connected DIG_IOx and SYS_EN pins.
    [oresatt-batteries.brd, oresatt-batteries.sch]
2017-06-23 Fixed Shutdown Circuit, Added more ground pins, cleaned up schematic
    [oresatt-batteries.brd, oresatt-batteries.sch]
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2017-06-23 Named missing NETS
    [oresatt-batteries.brd, oresatt-batteries.sch]
2017-06-23 Replaced Shutdown with new circuitry that will actually work... maybe.
    [oresatt-batteries.brd, oresatt-batteries.sch]
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2017-07-07 Fixed V- pin on STC
    [oresat-batteries.brd, oresat-batteries.sch]
2017-07-07 Fixed TP non-connect issue
    [oresat-batteries.brd, oresat-batteries.sch, oresatt-batteries.sch]
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2017-07-11 Cleaned up schematic, reverted to previous configuration for ADP
    [oresat-batteries.brd, oresat-batteries.sch]
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2017-09-23 Added charge and discharge control, lowside shutdown, test points and finished rough v1.1 design.
    [oresat-batteries-v1.1.brd, oresat-batteries-v1.1.sch]
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2017-09-28 Fixed most of the issues from design review Sept 25.
    [oresat-batteries-v1.1.brd, oresat-batteries-v1.1.sch]
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2017-11-18 Moved to OSH Park 4 layer DRU, fixed some bad/useless layers.
    [oresat-batteries-v1.1.brd]
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2018-03-15 First cleanup of batteries post-Austin going to NASA. Austiiiiinnnnnnnnn, come backgit diff ../design.mdn111git diff ../design.mdn./run More sane two sheet layout on schematic, cleaned up in and out 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
    [oresat-batteries-v1.1.brd, oresat-batteries-v1.1.sch, oresat-batteries.brd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]
2018-09-24 Fixed body diode issue on output. Changed N to P mosfett for 'trace heater.'
    [oresat-batteries.brd, oresat-batteries.sch]
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2019-03-23 Last changes to previous 1 cell battery pack. Abandoning for 2 cell packs because we're weenies.
    [oresat-batteries.brd, oresat-batteries.sch]
2019-03-23 New 2S2P battery boards, based on 18650 cells along with a BQ28400 battery IC.
    [oresat-batteries.brd, oresat-batteries.sch]
2019-07-29 update schematic with s8209 and MAX17205 chips for battery protection and control
    [oresat-batteries.brd, oresat-batteries.sch]
2019-07-29 Design review of schematic. Added labels, nets to M0, shutdown circuitry, discussed power domains.
    [oresat-batteries.brd, oresat-batteries.sch]
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2019-08-02 handing over to andrew for design review, still needs newest MCAD dxf for inhibit switches
    [oresat-batteries.brd]
2019-08-06 Updated battery board to latest outline (via oresat-cards.lbr), fixed ground planes, fixed main connector, done for now.
    [oresat-batteries.brd, oresat-batteries.sch]
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2019-08-12 added state diagram, more datasheets, starting moving from 2S2P to 2S1P packs
    [oresat-batteries.brd, oresat-batteries.sch]
2019-08-15 version 2.0 of battery card, moved to 2S1P packs, extra battery charge and fuel gauge circuitry, moved to 4 layer board
    [oresat-batteries.brd, oresat-batteries.sch]
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2019-12-29 New battery schematic and board. New Ablic and SD topology, with battery disconnect circuitry. Updated to Microcontroller and OPD v3.4.
    [oresat-batteries.brd, oresat-batteries.sch]
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2020-04-16 Latest OreSat battery board form factor, working with Oleg. Now with less tabs, and more slots, and more room
    [oresat-batteries.brd, oresat-batteries.sch]
2020-04-17 Latest battery holder DXF with more simple layout and more thermal resistance to frame. Updated battery circuitry from try #3 of the battery prototype. Only one pack layed out, checking in anyway.
    [oresat-batteries.brd, oresat-batteries.sch]
2020-04-18 Battery board v1 schematic and layout complete. Lots of checking and polishing left to do, but OMG, finally.
    [oresat-batteries.brd, oresat-batteries.sch]
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2020-04-18 More cleanup; added more space in battery tab stitching, and made them hopefully more sane?
    [oresat-batteries.brd, oresat-batteries.sch]
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2020-08-03 Some feedback from design review; more text, 100k instead of 10k for some transistors, still missing heaters.
    [oresat-batteries.brd, oresat-batteries.sch]
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2020-08-17 Updated README, killed design documents. Also, finished layout. Still need to polish, but heater is layed out and doesn't seem to be terrible.
    [oresat-batteries.brd, oresat-batteries.sch]
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2020-08-25 Added tolerance note to heaters.
2020-08-29 fixed a couple left over attributes and formatted BOM
    [oresat-batteries.brd, oresat-batteries.sch, oresat-battery-card-bom.xlsx]
2021-03-01 OreSat Battery Card v2.0
    Changes based on finally fixing the C3 watchdog timer and the interactions between the two.
    - Moved right hand ground cut switch to vbat switch. This solves a *lot* of problems with removing the ground and shutdown not working correctly.
    - Got rid of "fast charge" and split the charge / discharge paths with independent PTC (5A out, 2A in).
    - Switched most everytthing to 100k. 1M wasn't enough to overcome leakage, and 10k was too much.
    - Fixed the ablic bypass cap which should have gone right to VDD.
    - Rerouted !SD for lots of paranoia.
    - Rev'd board to v2.0
    - Changed to latest OreSat card outline (v1.3).
    [oresat-batteries.brd, oresat-batteries.sch]
2021-03-01 Full update of the BOM; added non PCB materials including the heaters, thermistors. Updated fuses to be decent PTCs. Might regret that later, but it really seems like the right thing.
    [oresat-batteries.brd, oresat-batteries.sch, oresat-battery-card-bom.xlsx]
2021-03-17 Upped battery board to v2.1. No real changes, besides adding fiducials (blargh!), updating the board version, and adding the flight marker to TPLACE.
    More importantly, the BOM has been upadated to reflect what Screaming Circuits is going to stuff for us.
    [oresat-batteries.brd, oresat-batteries.sch, oresat-battery-card-bom.xlsx]
2021-03-27 Updated shutdown mosfet resistors to 100k after the battery failed quiescent power draw, and removed backup thermistors from the BOM.
    [oresat-batteries.brd, oresat-batteries.sch, oresat-battery-card-bom.xlsx]
2021-04-09 OreSat Battery Card v2.1
    - Shrunk fastener foot prints to gain more room.
    - Redid DF3 switch layouts to get the jumper wires closer to the switche's mini-contact holes.
    - Added fiducials.
    - Replaced quad N channel MOSFET with four N channels because the quad pack is unobtainium right now.
    [oresat-batteries.brd, oresat-batteries.sch, oresat-battery-card-bom.xlsx]
2021-04-20 Fixed off by one on BOM
    [oresat-battery-card-bom.xlsx]
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2021-11-09 v3.0 sent off to fab! Updated BOM, and committed final changes to card. Lots of small changes, including better power routing, resistors in the UART line to the C3, and as mentioned in an earlier com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
    [oresat-batteries.brd, oresat-batteries.sch, oresat-battery-card-bom.xlsx]
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2022-01-28 Updated inhibit switch diagram to be more compact, reflect Nanoracks SDT call outs
    [oresat-batteries-inhibits-blockdiagram.sch]
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2022-07-28 Fixed a ton of DRC errors, maybe found some problems
    [Battery_Pack_1_(BOTTOM).kicad_sch, Battery_Pack_2_(TOP).kicad_sch, Connectors%2fMCU.kicad_sch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]
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2022-07-29 Fixed the voltage regulator problem, and the DRC is happy
    [Connectors.kicad_sch, Power.kicad_sch, oresat-batteries.kicad_sch]
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2023-12-02 Updating KiCAD import of EAGLE battery card v3.0 and calling it v3.1 because the gerber files will definitely be different and we'll probably implement a few small changes. Reimports, renames, and fi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
    [Battery_Pack_1_(BOTTOM).kicad_sch, Battery_Pack_2_(TOP).kicad_sch, Connectors%2fMCU.kicad_sch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]
2023-12-02 Maybe it's better if there's not an extra copy of the KiCAD import files?
    [Battery_Pack_1_(BOTTOM).kicad_sch, Battery_Pack_2_(TOP).kicad_sch, Connectors%2fMCU.kicad_sch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]
2023-12-02 Kicad import try #3. Now with DXFs from custom EAGLE layers. Schematic worksheets and names updated.
    [oresat-batteries-sch-Connectors.kicad_sch, oresat-batteries-sch-connectors.kicad_sch, oresat-batteries-sch-mcu.kicad_sch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]
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2023-12-02 Transferred connector page to oresat-kicad. Added correct card outline.
    [oresat-batteries-sch-connectors.kicad_sch, oresat-batteries-sch-microcontroller.kicad_sch, oresat-batteries-sch-pack-1.kicad_sch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]
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2023-12-03 better schematic layout (no netlist changes) on battery packs, and updated DRUs and fixed some minor DRU issues.
    [oresat-batteries-sch-microcontroller.kicad_sch, oresat-batteries-sch-pack-1.kicad_sch, oresat-batteries-sch-pack-2.kicad_sch]
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2026-01-11 Starting Battery Card 4.0
    Changed root sheet to hierarchical sheet. No change to schematic or layout yet. Updated the stackup with oresat template. Switched to variables for version and date.
    [oresat-batteries-sch-connectors.kicad_sch, oresat-batteries-sch-heater.kicad_sch, oresat-batteries-sch-microcontroller.kicad_sch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]
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2026-01-14 Renovated Schematic
    Updated schematic symbols and made more uniform with changed resistor, capacitor, and FET symbols. Changed 0603 cap foot print to 0603 small in Oresat passives. Added 2 new resistors and 2 new caps i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
    [oresat-batteries-sch-heater.kicad_sch, oresat-batteries-sch-microcontroller.kicad_sch, oresat-batteries-sch-pack-1.kicad_sch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]
2026-02-01 Progress on v4
    Figure out to bypass negative battery cutoff with 10k to make sure that nSHUTDOWN always works. Lots of moving around (it's tight), finally got pack 1 done. Working on the Pack 2.
    [oresat-batteries-sch-heater.kicad_sch, oresat-batteries-sch-pack-1.kicad_sch, oresat-batteries-sch-pack-2.kicad_sch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]
2026-02-02 Progress on battery card v4
    Moved in -batt cutoffs, which caused a lot of pain and suffering. Started updating BOM, and fixed all transistor packages. Updated resistor packages, too. Still needs a lot of cleanup, but probably 80% done now.
    [oresat-batteries-sch-heater.kicad_sch, oresat-batteries-sch-microcontroller.kicad_sch, oresat-batteries-sch-pack-1.kicad_sch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]
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2026-03-23 Updated data, spiffed up the root page, renamed some STM specific OPD signals, synced SCH and BRD, fixed a bunch of DRC errors, NOW ready for MCXN import that will screw everything up.
    [oresat-batteries-sch-heater.kicad_sch, oresat-batteries-sch-microcontroller.kicad_sch, oresat-batteries-sch-pack-1.kicad_sch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]
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2026-04-05 Routed unconnected lines - needs DRC fixes and review
    [oresat-batteries.kicad_pcb]
2026-04-05 Cleaned Up DRC errors & silkscreen
    Should be good? Needs review. Only 2 warnings left, "isolated copper fill" for zones Q36-D etc...
    [oresat-batteries.kicad_pcb]
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
